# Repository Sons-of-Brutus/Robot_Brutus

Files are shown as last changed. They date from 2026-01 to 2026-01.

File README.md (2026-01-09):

# Robot Brutus

This repository contains the final project for the Mechatronics course, part of the Degree in Software Robotics Engineering at the Rey Juan Carlos University.

**Authors:** Sergio Sanchez Hernandez, Jorge Barroso Saugar, Sergio Cobos Blanco

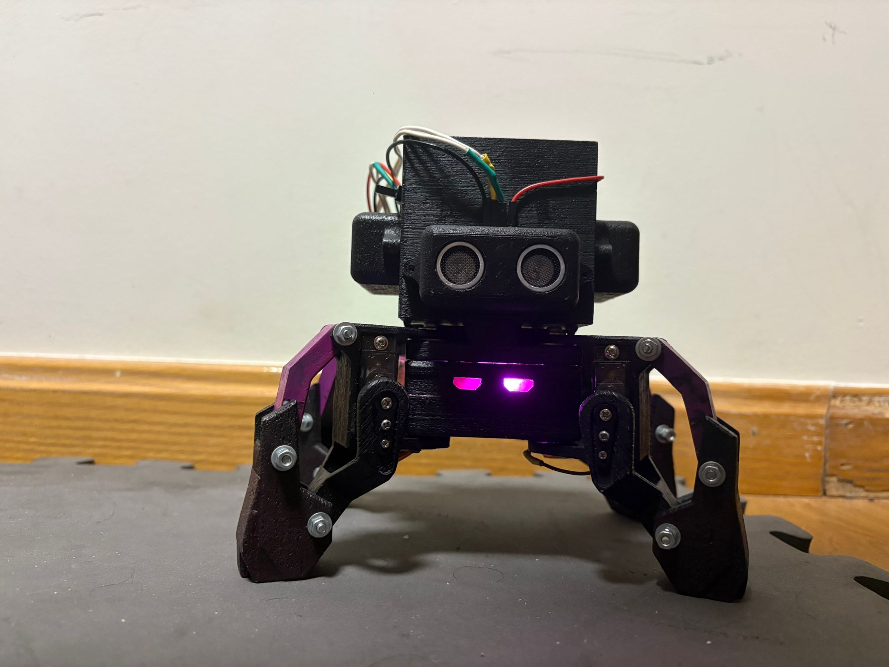
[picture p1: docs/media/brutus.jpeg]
BRUTUS


What can you find in this repository:
- [Technical report](./docs/brutus_technical_report.pdf)
- [User and mantainance manual](./docs/user_and_mantainance_manual.md)
- [Meshes of the pieces](./meshes/)
- [Code](./src/brutus_esp32)
- [Brutus' MQTT user interfaces](./mqtt_interface/)
- [Doxygen index of the code](https://sons-of-brutus.github.io/Robot_Brutus/)

---

Original design from thingiverse: https://www.thingiverse.com/thing:1265766/files

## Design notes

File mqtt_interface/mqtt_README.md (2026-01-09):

# mqtt_README

Brief guide to install Mosquitto and test MQTT topics (public broker: `test.mosquitto.org`).

## Requirements
- Debian/Ubuntu based system
- Internet connection (a public broker is used for testing)

## 1. Install Mosquitto and clients
```bash
sudo apt update
sudo apt install mosquitto mosquitto-clients -y
```

## 2. Subscribe to individual topics
Open a terminal for each subscriber (or multiplexer if you prefer).

ESP (topics published by the ESP32):
```bash
mosquitto_sub -h test.mosquitto.org -t brutus/data/heartbeat
mosquitto_sub -h test.mosquitto.org -t brutus/data/pose
mosquitto_sub -h test.mosquitto.org -t brutus/data/distance/front
mosquitto_sub -h test.mosquitto.org -t brutus/data/distance/right
mosquitto_sub -h test.mosquitto.org -t brutus/data/distance/left
```

Controller (topics received/monitored by the controller):
```bash
mosquitto_sub -h test.mosquitto.org -t brutus/cmd/mode
mosquitto_sub -h test.mosquitto.org -t brutus/cmd/velocity
mosquitto_sub -h test.mosquitto.org -t brutus/cmd/pose
```

## 3. Subscribe to all topics
Use the wildcard `#` to capture everything under `brutus/`:
```bash
mosquitto_sub -h test.mosquitto.org -t "brutus/#"
```

## 4. Publish test messages
Send test messages to verify callbacks and subscriptions.

Messages from the ESP (simulated):
```bash
mosquitto_pub -h test.mosquitto.org -t brutus/data/heartbeat -m "heartbeat"
mosquitto_pub -h test.mosquitto.org -t brutus/data/pose -m "data_pose"
mosquitto_pub -h test.mosquitto.org -t brutus/data/distance/front -m "sensor_front"
mosquitto_pub -h test.mosquitto.org -t brutus/data/distance/right -m "sensor_right"
mosquitto_pub -h test.mosquitto.org -t brutus/data/distance/left -m "sensor_left"
```

Messages from the controller:
```bash
mosquitto_pub -h test.mosquitto.org -t brutus/cmd/mode -m "cmd_mode"
mosquitto_pub -h test.mosquitto.org -t brutus/cmd/velocity -m "cmd_vel"
mosquitto_pub -h test.mosquitto.org -t brutus/cmd/pose -m "cmd_pose"
```

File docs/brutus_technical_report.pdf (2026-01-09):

# Brutus: Design and Implementation of a Quadruped Robot


Sergio Sanchez Hernandez, Jorge Barroso Saugar, Sergio Cobos Blanco

January 2026

1

## Contents

1 Introduction | 3
2 Structural Design | 3
3 Electronic design | 4
4 Software and control | 8
5 Software Implementation | 8
6 Simulation and Design Validation | 9
7 Experimental Results: Wall-Following Test | 10
8 Future Work and Proposed Improvements | 10

2

## 1 Introduction

This technical report details the design and implementation of the Brutus quadrupedal robot, providing an in-depth analysis of its structural design, hardware specifications, and FreeRTOS-based embedded software control.
The robot must meet the following specifications:
- Its dimensions must not exceed 30 × 30 × 30 cm.
- It must be powered by rechargeable batteries.
- The robot must feature a basic interface to start and stop its operation.

It must also pass the following two tests:

- Wall-Following Test: In less than 1 minute, the robot must move parallel to a flat wall, placed on either side of the robot, for at least 1 meter. Additionally, it must carry a 250-gram load.
- Obstacle Avoidance Test: In less than 2 minutes, the robot must be capable of avoiding obstacles while moving within a 2 × 2 meters area, reaching each of the adjacent walls. The robot starts from the center of the square.

## 2 Structural Design

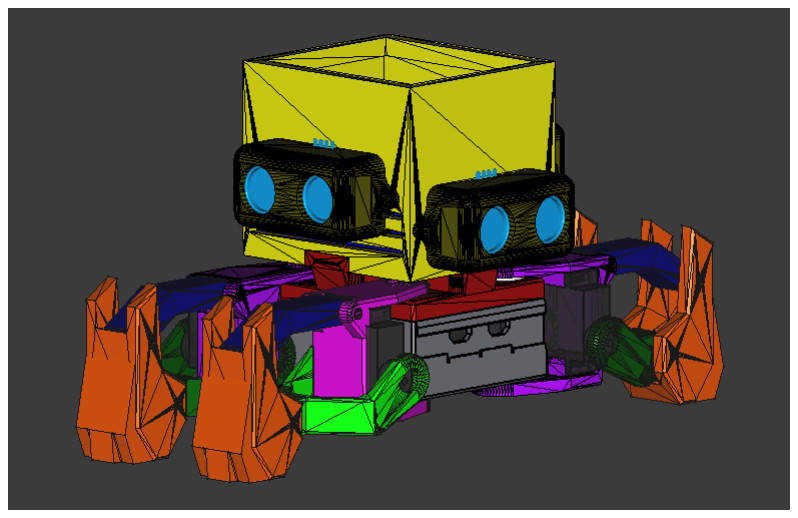
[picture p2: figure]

Figure 1: Full assembly of the Brutus robot in FreeCAD.

### 2.1 Design selection and justification

The design of Brutus is based on a model found on Thingiverse. (https://www.thingiverse.com/thing:1265766/files)

This design was selected for its compact footprint, ensuring full compliance with the size specifications and less effort for the servos at the joints. Additionally, the two degrees of freedom in each of the four legs allow for simplified control while maintaining high mobility standards.

3

One of the most remarkable features of this design is the parallel linkage mechanism incorporated into the legs. This configuration ensures that the foot remains perpendicular to the ground throughout its vertical range of motion. Consequently, onboard sensors are isolated from tilt variations along the X and Y axes, maintaining a stable reference frame during locomotion.

### 2.2 Comparison with Original Design

The original models underwent several aesthetic and practical modifications to suit the project requirements:

- Both the ’shoulders’ and the chassis were modified to accommodate MG90s servo motors.
- A custom top module was designed to house the power supply battery and circuit, and distance sensors.
- The chassis cover was redesigned to attach the upper module (upside) and the ESP32 (facing down).

### 2.3 Materials and Manufacturing

The structural components were manufactured using 3D printing. PLA was selected as the primary material due to its high tensile strength, ease of printing, and dimensional stability, which is critical for the alignment of the leg mechanisms.

## 3 Electronic design

### 3.1 Actuators

The selected actuators must therefore provide sufficient torque, adequate speed, electrical compatibility and acceptable size and weight.

The servos must be capable of:

- Supporting the weight of the robot and the load during the support phase of walking.
- Producing enough torque to lift and move the legs.
- Moving fast enough to generate a stable and smooth gait.
- Allow PWM control.

4

The robot uses MG90S micro servos for all leg joints. Small, lightweight, strong and fast-rotation actuators, which are a really good election for the robot.

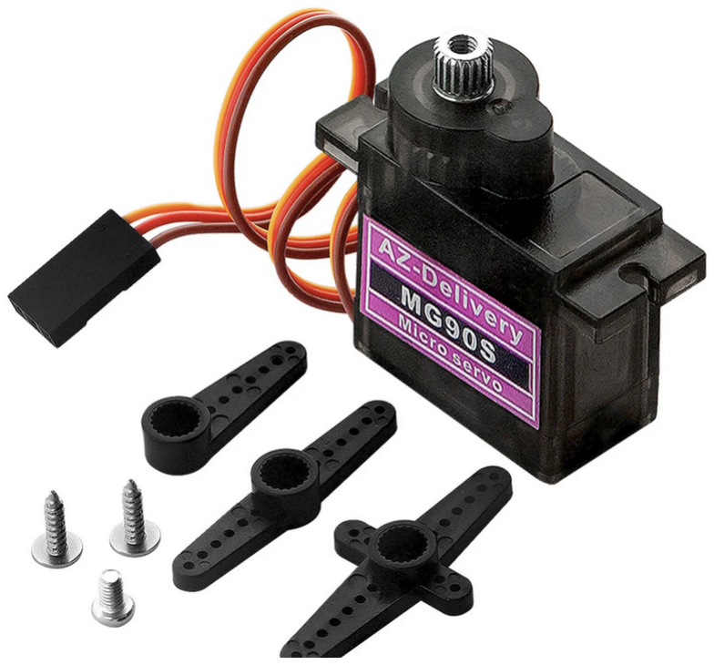
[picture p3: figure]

Figure 2: MG90s servo

The MG90S servo provides a nominal stall torque of approximately 1.86 kg · cm, which correspond to 0.1824 N
m .

The typical speed of this servos is 0.1 s/600◦
, so we know that they can reach 600◦/s ≈ 10.47 rad/s. This ensures that the simulated gait is realistic and achievable by the real servos. The MG90S provides sufficient speed to generate a smooth and stable walking motion without causing excessive inertia or oscillations.

The 8 servos are controlled using a PCA9685. This is a 16-channel, 12-bit PWM I2C-bus controlled driver that significantly offloads the processing work from the main microcontroller. By using this external driver, we can control all 8 servomotors using only two pins (SDA and SCL), which simplifies the wiring and ensures high-precision timing for the leg movements.

The final actuator is an RGB LED module, which serves as a visual diagnostic tool. This component enables real-time debugging by representing up to eight distinct color combinations, allowing for the intuitive monitoring of various system states and logic conditions.

### 3.2 Sensors

The sensors selected for resolving the exercises were the HC-SR04 for distance measurement. These are cost-effective ultrasonic sensors that operate by emitting high-frequency sound waves and measuring the time it takes for the echo to return after hitting an object.

5

With a detection range of ≈ 2 cm to 400 cm and an accuracy of ≈ 3 mm, this small sensors are ideal for the Wall-Following and Obstacle Avoidance tests. In our configuration, three sensors were mounted on the custom top module, facing front, left, and right, to provide a 180◦ field of view, allowing the Brutus robot to maintain a constant distance from the walls while simultaneously detecting potential collisions in its path.

### 3.3 Control unit

The ESP32-WROOM-32 was selected as the central processing unit due to its superior technical specifications. Its dual-core architecture enables the isolation of the gait control algorithm from perception and high-level logic tasks, ensuring stable locomotion. Integrated WiFi and Bluetooth connectivity facilitate remote commanding and real-time telemetry via an external web interface.

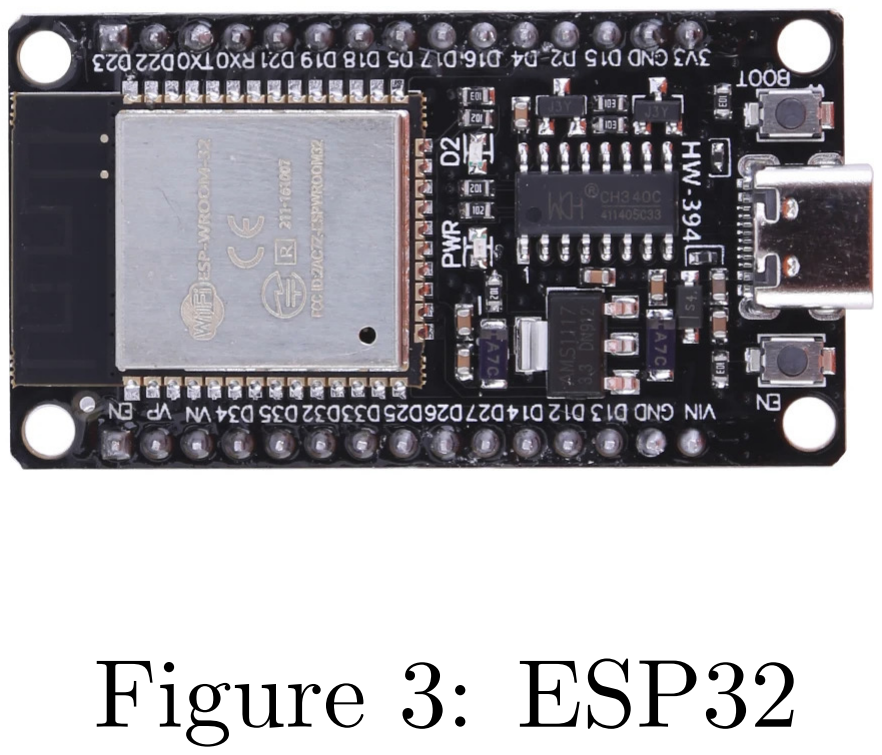
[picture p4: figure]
Figure 3: ESP32

Furthermore, its high clock speed and memory capacity provide a significant performance advantage over traditional platforms like Arduino UNO. The native support for FreeRTOS is crucial for implementing Brutus as a Real-Time System (RTS), allowing for deterministic task scheduling. Finally, its compact form factor ensures a seamless fit within the chassis constraints.

### 3.4 Power supply unit

Total current (peak and continuous) required by the system:

IT = IESP 32 + IHC−SR04 × 3 + ILED + IMG90s × 8 + IP CA9685

Ipeak ≈ 0.3 + 0.015 × 3 + 0.06 + 1.1 × 8 + 0.025 = 9.23 A
Icontinous ≈ 0.3 + 0.002 × 3 + 0.06 + 0.4 × 8 + 0.025 = 3.29 A

We want Brutus to operate for at least half an hour, so the minimum required capacity in the worst case must be:
qT = 9.23 A × 0.5 h = 4.615 Ah = 4615 mAh

These are the components (with their nominal voltage) which will be powered by the battery:

- ESP32 (5 V)

6

- PCA9685, and servos connected to it (5 V)
- HC-SR04 (5 V)

Our battery has to give 5 V.

The selected battery is a 3S1P Li-ion battery (12 V, 5200 mAh) was chosen because it satisfies all the electrical, power and autonomy requirements of the robot while remaining compact and lightweight. This battery has a discharge continous current of 5 A and a discharge peak current of 10 A.

If we consider the “worst case” as a sustained demand close to the battery’s continuous current rating:
Tworstcase(peak) = 5.2/9.23 = 0.56 h ≈ 33.6 min
Tworstcase(continuous) = 5.2/3.29 = 1.58 h ≈ 45.6 min

The battery provides a voltage range of 8.0 V to 12.6 V, so we choosed to use a DC-DC Buck Module to generate a stable 5 V supply for all electronics regardless of the battery’s state of charge.

### 3.5 Electronic Schematic

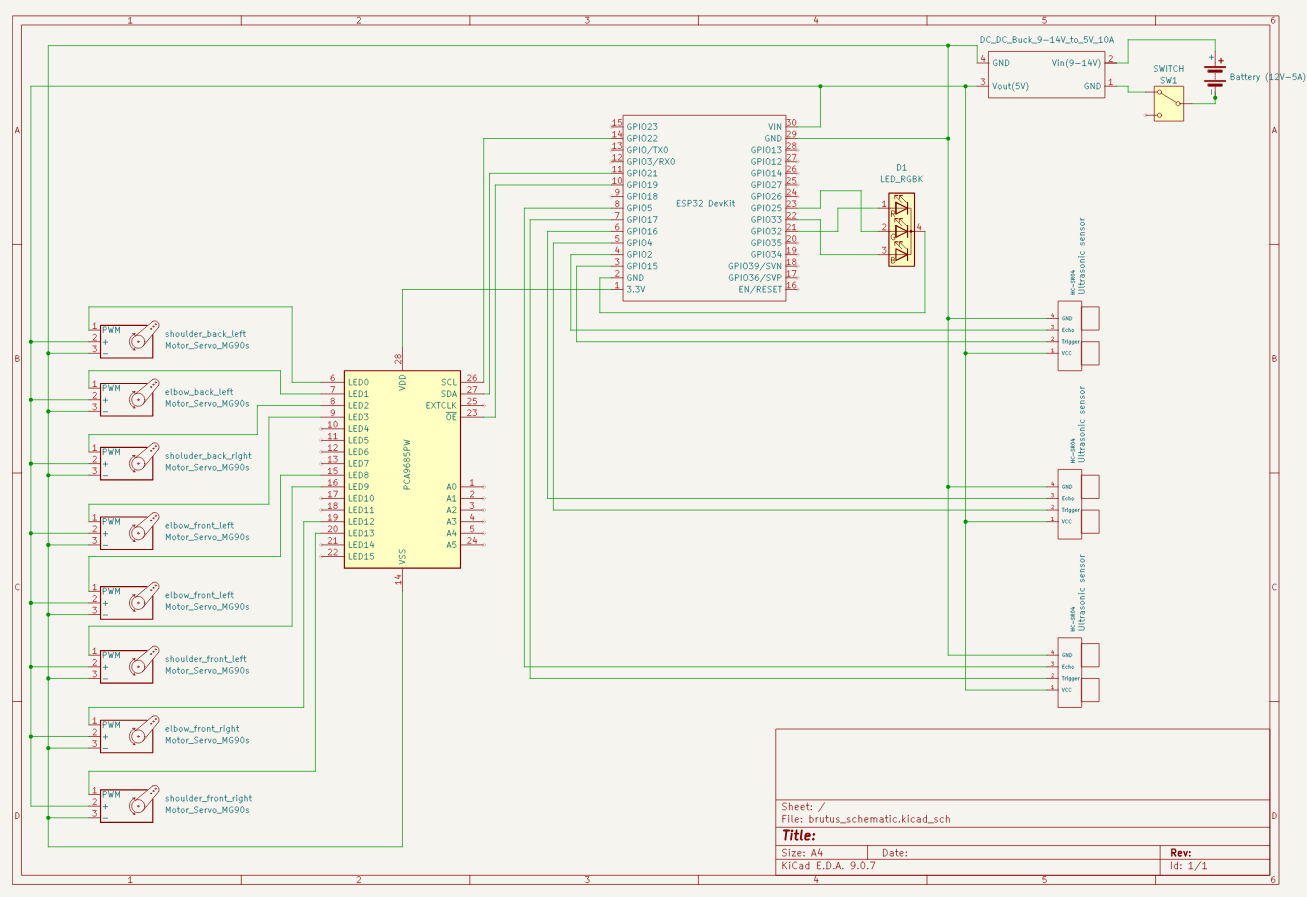
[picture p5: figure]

Figure 4: KiCad schematic of the circuit

7

## 4 Software and control

## 5 Software Implementation

The robot’s firmware is built upon FreeRTOS, enabling its operation as a Real-Time System (RTS) and ensuring deterministic execution of all critical tasks. Leveraging the dual-core architecture of the ESP32, the locomotion control is isolated on one core, while perception, high-level logic, and communication protocols run independently on the second.
The primary codebase is developed using Object-Oriented Programming (OOP) within the Arduino framework, establishing a modular and scalable architecture. The system is structured through the following specialized classes:
- Pca9685Servo.h: A low-level interface for direct pulse-width modulation (PWM) control via the PCA9685 driver.
- BrutusLegInterface.h: A kinematic abstraction layer for individual leg positioning (dependent on Pca9685Servo.h).
- BrutusPerception.h: This class manages the operation of the HC-SR04 ultrasonic sensors.
- Brutus.h: A comprehensive manager for the robot’s global state, coordinating all integrated actuators and sensors (dependent on BrutusLegInterface.h and BrutusPerception.h).
- BrutusComms.h: A dedicated interface for asynchronous MQTT-based communications.

### 5.1 Locomotion and Gait Algorithm

The locomotion strategy is based on a diagonal trot gait, characterized by a sequence of poses where two diagonal pairs of legs move in synchronization. While one pair performs the swing phase (moving through the air), the opposite pair executes the stance phase (contact with the ground), providing the necessary thrust to propel the chassis forward.
For high-level maneuvering, a velocity-based control scheme was implemented. This allows the system to translate linear velocity commands (vx) and angular velocity commands (ω) into coordinated joint movements:
- Translation: Achieved by modulating the step frequency and stride length.
- Rotation (Yaw Control): Instead of complex inverse kinematics, an efficient differential thrust method was used. By reducing the angular sweep (amplitude) of the ”shoulder” servos on the inner side of the turn, the outer legs generate a larger displacement vector, effectively pivoting the robot toward the desired direction.

8

### 5.2 Remote Interface and Telemetry

Brutus maintains a persistent connection to an MQTT broker, facilitating real-time telemetry, state switching, and remote commanding. To satisfy the requirement for a visual user interface, both a native Android application developed in Android Studio and a custom CLI (Command Line Interface) script were implemented, allowing for seamless interaction with the robot’s internal states.

### 5.3 Concurrency and Thread-Safety

Perception is handled by a periodic FreeRTOS task that samples ultrasonic distance data. To ensure data integrity in a multi-core environment, these values are accessed via thread-safe methods protected by Binary Semaphores (Mutexes). This synchronization mechanism prevents race conditions when the high-level logic task requests sensor data while the perception task is updating it. Similar protection is applied to the velocity command variables. The priorities for the multi-task core are: 1. Perception, 2. High-Level logic, 3. Communications.

## 6 Simulation and Design Validation

The primary objective of the simulation was to validate the robot’s stability, center of mass (CoM), and joint torque requirements through a detailed URDF model. Realistic mass and inertia properties were assigned to each link, including the external load on the top module, to ensure the physical design could withstand operational stresses and maintain coherent kinematics before manufacturing.
Due to the complexity of closed-loop
kinematic chains in physics engines,
the parallel linkage was simplified in the URDF while functionally maintaining foot perpendicularity. This causes a not really realistic analysis of the torques and the movement. The servomotors were modeled using position control with real-world torque and speed limits (600◦/s), enabling real-time logging to CSV files to verify that the selected actuators could handle peak loads during locomotion.

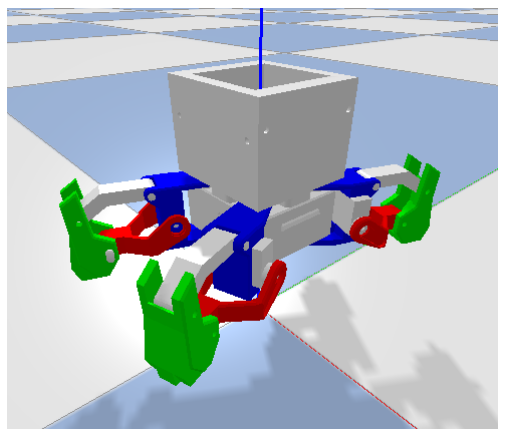
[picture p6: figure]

9

## 7 Experimental Results: Wall-Following Test

Figure 5 shows the optimal trial where the loaded robot traversed 1.6 meters. The right-hand sensor data reveals minor oscillations around the setpoint, caused by intrinsic noise, gait-induced mechanical shifts, and control logic tuning. Despite these fluctuations, the system demonstrated robust wall-following performance under loaded conditions.

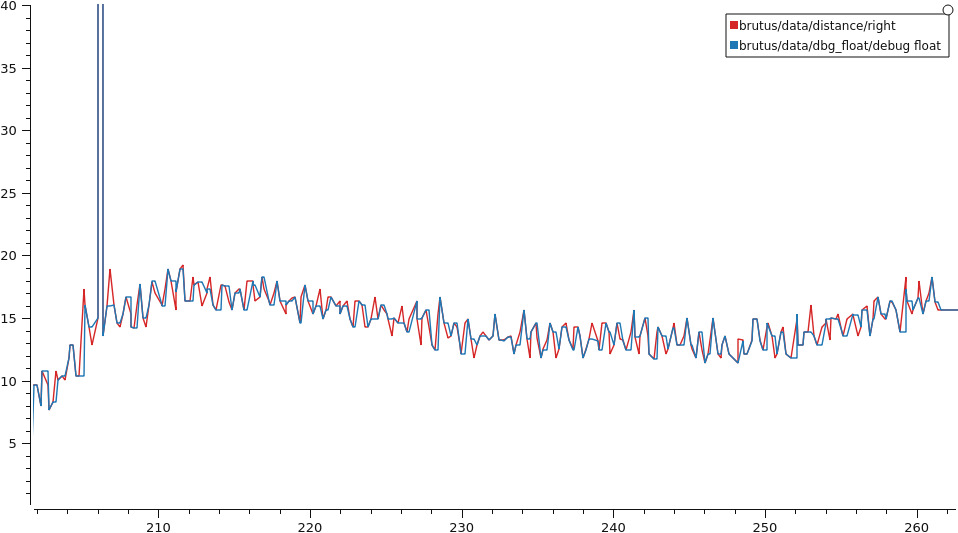
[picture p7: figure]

Figure 5: Ultrasonic sensor data during the 1.6-meter wall-following test.

## 8 Future Work and Proposed Improvements

- Sensor Fusion and Pose Estimation: Integrating an Inertial Measurement Unit (IMU) to implement filtering algorithms (such as a Kalman or Complementary filter). This would compensate for gait-induced oscillations during the swing phase and provide real-time data on the robot’s attitude (roll, pitch, and yaw), ensuring a stable reference frame for navigation.
- Active Perception (Scanning Radar): Mounting the ultrasonic sensors on dedicated micro-servos to implement an active scanning radar system. This configuration would significantly expand the Field of View (FoV), allowing for the generation of local occupancy maps and improving obstacle detection and path planning in complex environments.
- Structural Optimization for Serviceability: Expanding specific chassis sections to enhance thermal management through improved airflow. Additionally, redesigning the internal layout to increase accessibility, thereby facilitating assembly, cable routing, and routine maintenance procedures.

10

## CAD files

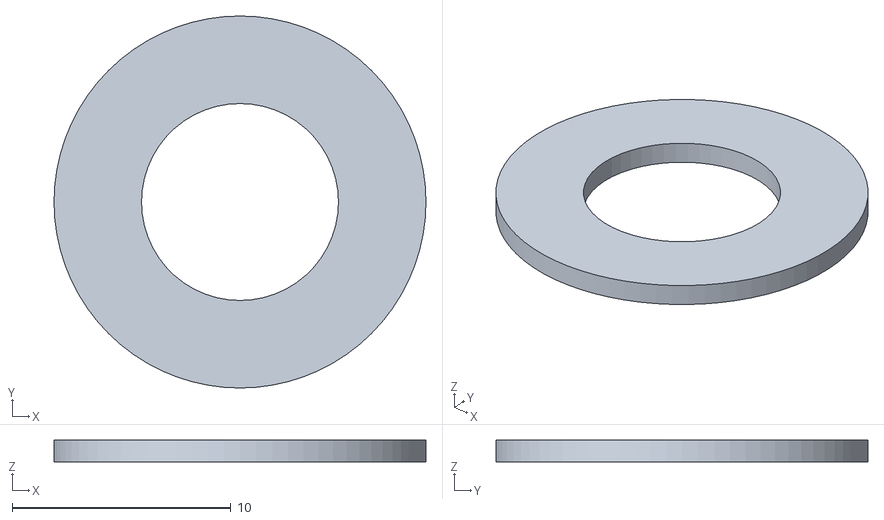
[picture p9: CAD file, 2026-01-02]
meshes/spacer.stl
17.0 x 17.0 x 1.00

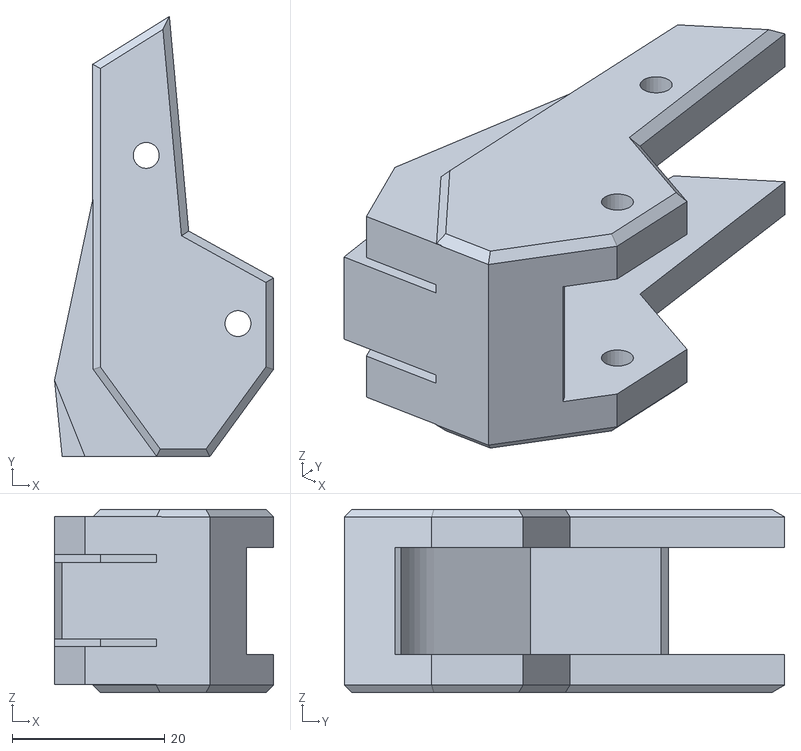
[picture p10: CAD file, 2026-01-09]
simulation/pybullet/model/meshes/foot_fist_mesh_relocated.stl
28.6 x 57.6 x 24.0

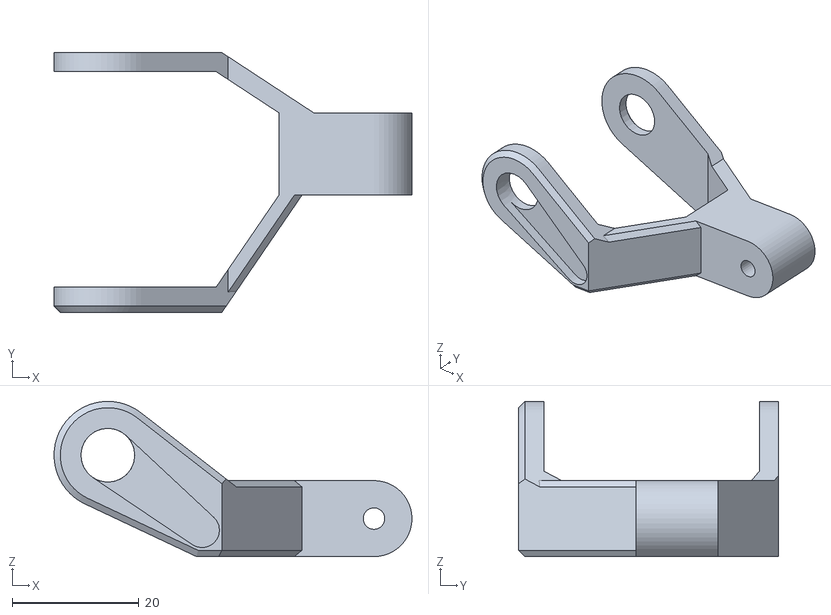
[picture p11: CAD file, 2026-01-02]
meshes/left_elbow_mesh.stl
56.5 x 41.0 x 24.5

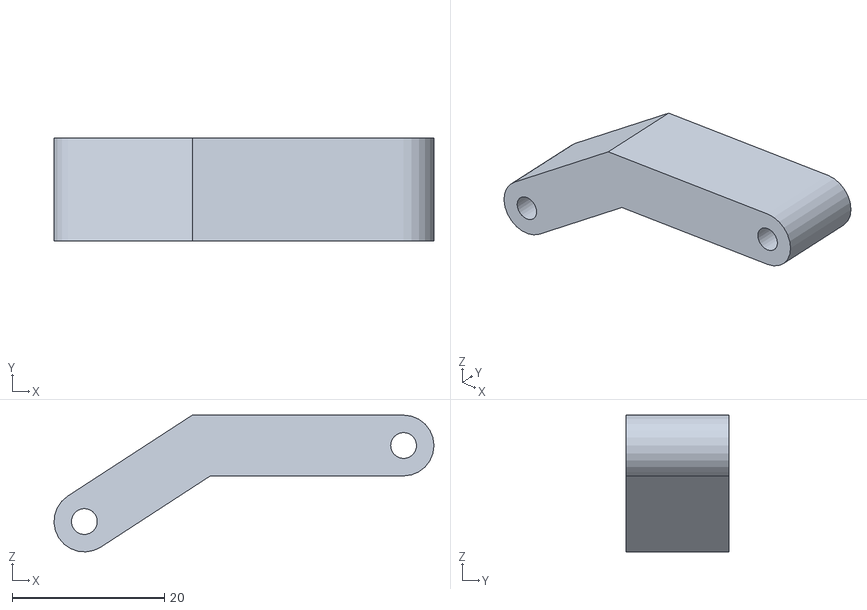
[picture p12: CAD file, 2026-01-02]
meshes/leg_up_link_mesh.stl
50.0 x 13.5 x 18.0

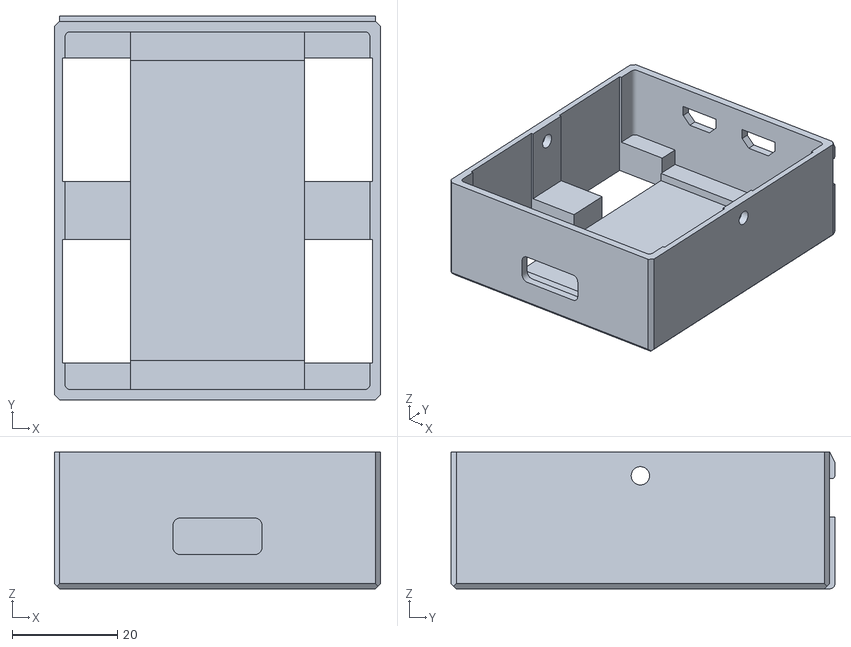
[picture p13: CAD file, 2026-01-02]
meshes/chasis_mesh.stl
62.0 x 73.0 x 26.0

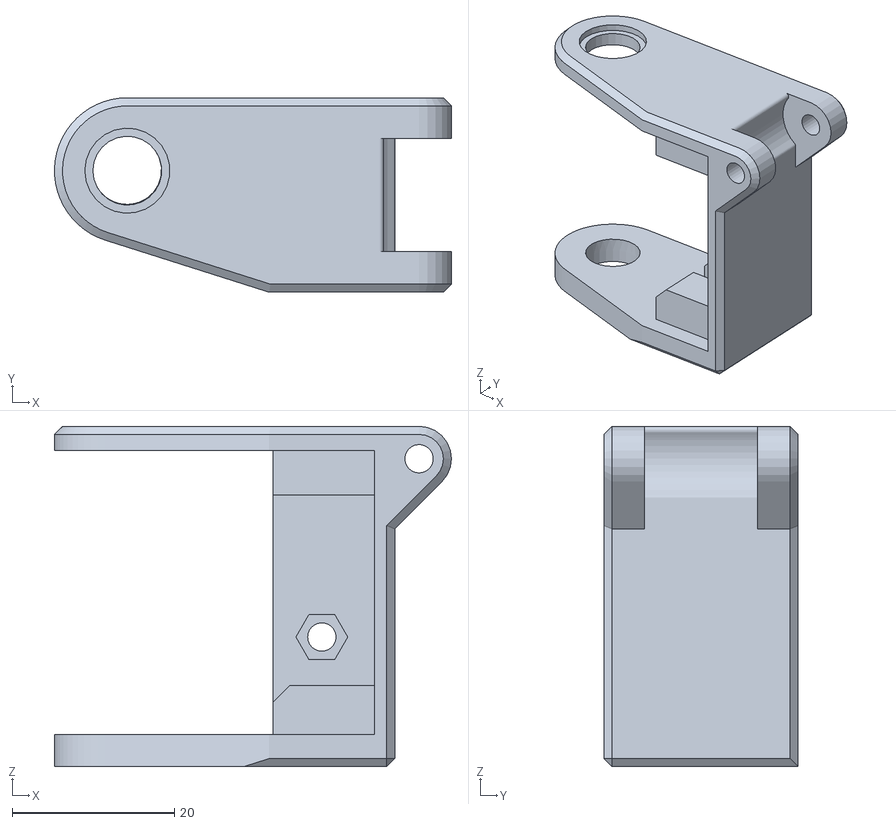
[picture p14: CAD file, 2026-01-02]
meshes/left_shoulder_mesh.stl
49.0 x 24.0 x 42.0

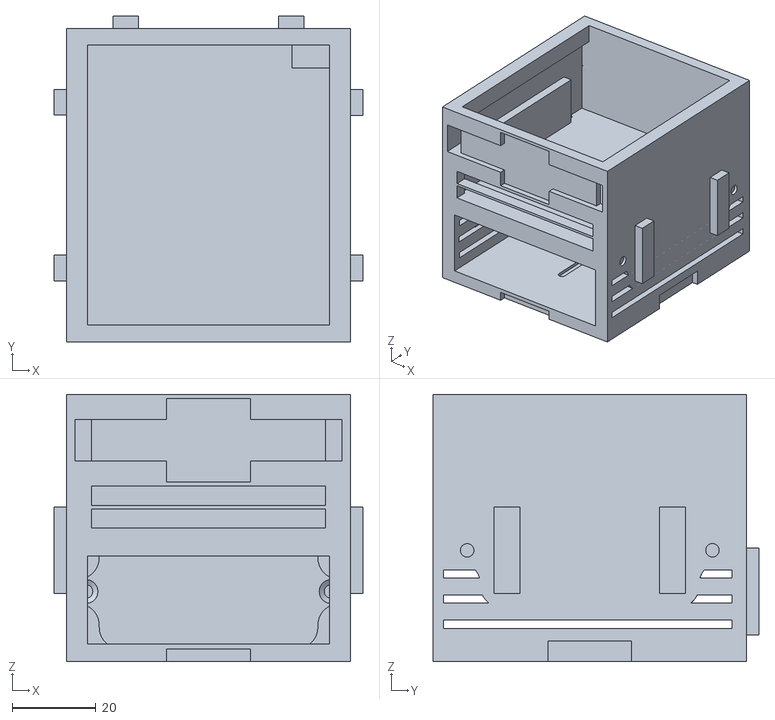
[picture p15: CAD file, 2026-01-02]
meshes/up_box_mesh.stl
73.9 x 78.0 x 64.0

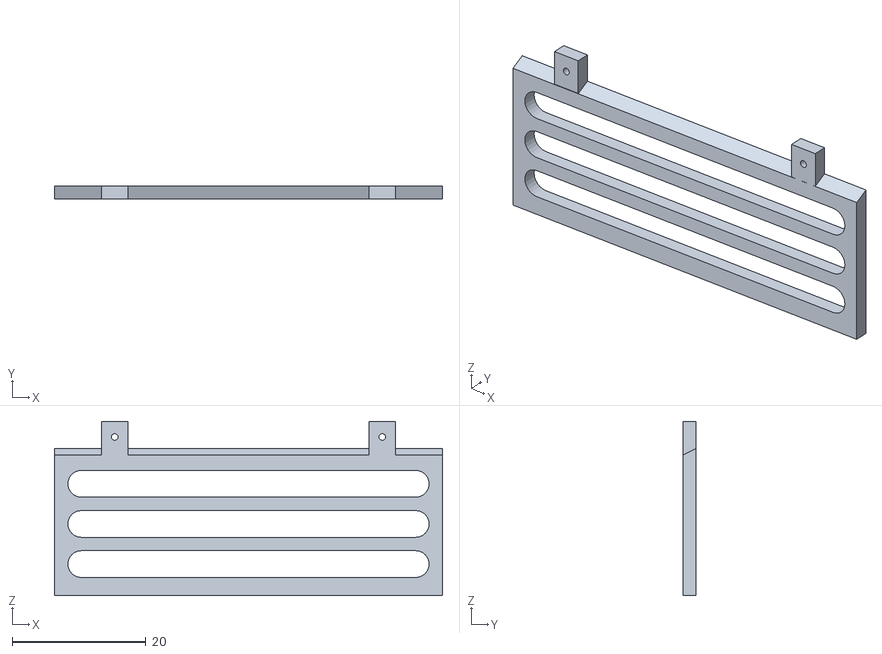
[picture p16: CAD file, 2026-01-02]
meshes/battery_limit_mesh.stl
58.0 x 2.00 x 26.1

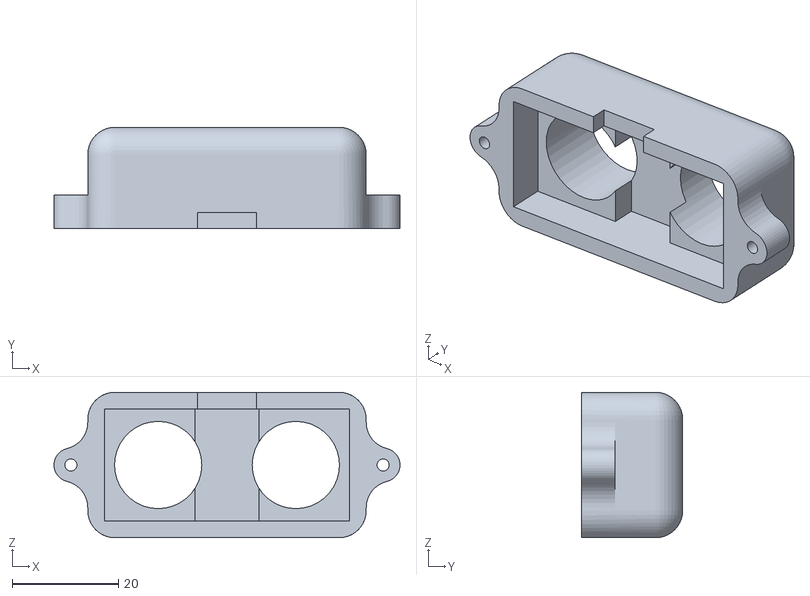
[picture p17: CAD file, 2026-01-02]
meshes/us_chasis_mesh.stl
65.0 x 19.1 x 27.3

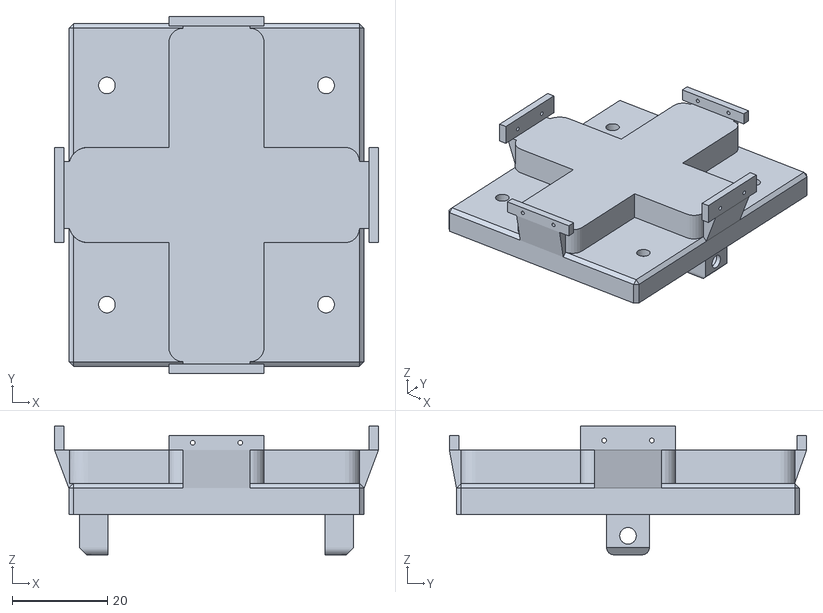
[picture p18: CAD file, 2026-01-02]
meshes/chasis_cover_mesh.stl
68.0 x 75.0 x 27.0

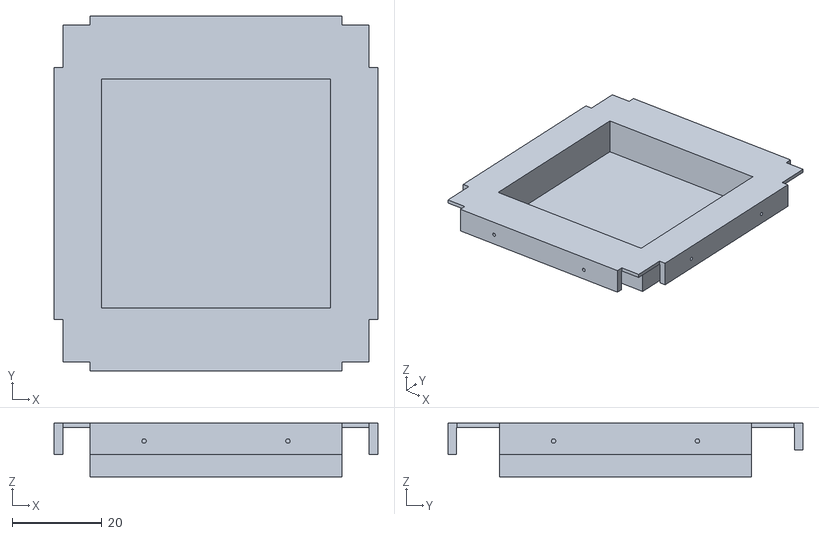
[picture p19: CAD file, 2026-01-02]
meshes/weight_case_mesh.stl
72.0 x 79.0 x 12.0

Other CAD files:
simulation/pybullet/model/meshes/foot_fist_mesh.stl
meshes/right_shoulder_mesh.stl
meshes/right_elbow_mesh.stl

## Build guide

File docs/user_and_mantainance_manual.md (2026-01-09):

# User and mantainance manual

---

## Table of content

This document is divided into the following sections:

1. [Mantainance manual](#mantainance-manual)
2. [Robot Components Overview](#robot-components-overview)
3. [Materials](#materials)
   1. [Printable pieces](#printable-pieces)
   2. [Electronic components](#electronic-components)
   3. [Wiring](#wiring)
   4. [Fasteners](#fasteners)
4. [Assembly](#assembly)
   1. [Soldering `ESP32` and `PCA9685` Connections](#1-soldering-esp32-and-pca9685-connections)
   2. [Assembling chasis (Part 1)](#2-assembling-chasis-part-1)
   3. [Assembling legs (Part 1)](#3-assembling-legs-part-1)
   4. [Connecting servos to `PCA9685`](#4-connecting-servos-to-pca9685)
   5. [Assembling chasis (Part 2)](#5-assembling-chasis-part-2)
   6. [Joining legs with chasis](#6-joining-legs-with-chasis)
   7. [Assembling upper box](#7-assembling-upper-box)
   8. [Joining upper box with chasis](#8-joining-upper-box-with-chasis)
   9. [Assembling legs (Part 2)](#9-assembling-legs-part-2)
5. [Mechanical Maintenance](#mechanical-maintenance)
   1. [Fasteners and Joint Inspection](#fasteners-and-joint-inspection)
   2. [Bearing Condition](#bearing-condition)
   3. [Servo Mounting and Horns](#servo-mounting-and-horns)
   4. [Printed Part Inspection](#printed-part-inspection)
6. [Battery Maintenance and Safety](#battery-maintenance-and-safety)
   1. [Voltage limits](#voltage-limits)
   2. [Storage recommendations](#storage-recommendations)
7. [Electrical Connections and Wiring Integrity](#electrical-connections-and-wiring-integrity)
   1. [Critical power cables](#critical-power-cables)
   2. [Connections most likely to cause power loss](#connections-most-likely-to-cause-power-loss)
   3. [Detecting bad contacts](#detecting-bad-contacts)
   4. [Ultrasonic sensor cables](#ultrasonic-sensor-cables)
8. [User Manual](#user-manual)
   1. [Network and MQTT configuration](#network-and-mqtt-configuration)
   2. [WiFi configuration](#wifi-configuration)
   3. [MQTT configuration](#mqtt-configuration)
9. [`brutus_params.h` – Robot configuration and motion parameters](#brutus_paramsh--robot-configuration-and-motion-parameters)
10. [`comms_params.h` – MQTT communication configuration](#comms_paramsh--mqtt-communication-configuration)
11. [User Sketch](#user-sketch)
12. [Logic Task Definition](#logic-task-definition)
13. [Doxygen](#doxygen)

---

# Mantainance manual

This document describes the recommended maintenance procedures for the Brutus quadruped robot.  
Its purpose is to ensure long-term reliability, safety, and performance by defining how the mechanical, electrical, and structural components should be inspected, cleaned, and replaced over time.

Brutus is a multi-servo quadruped robot built from 3D-printed structural parts, metal fasteners, electronic modules, and a Li-ion power system. Due to the presence of moving joints, electrical power distribution, and lithium batteries, proper maintenance is essential to prevent premature wear, electrical failures, and unsafe operating conditions.

This manual is based on:
- The mechanical assembly guide  
- The list of printed and electronic components  
- The electrical schematic (KiCad)  
- The battery and power system design  

It is intended for:
- Regular users performing routine checks  
- Developers modifying or upgrading the robot  
- Anyone disassembling and reassembling this robot  

The procedures described here allow safe servicing without damaging the robot.

---

## Robot Components Overview

Before performing any maintenance, inspection, or repair on Brutus, it is essential to understand the physical and electronic components that make up the robot.

This section provides a complete overview of all structural, mechanical, and electronic elements used in Brutus. Knowing the location, function, and role of each part allows safe and efficient troubleshooting, replacement, and upgrades.

---

## Materials

### Printable pieces
| Name | Quantity | Mesh | Image |
| :--- | :---: | :---: | ---: |
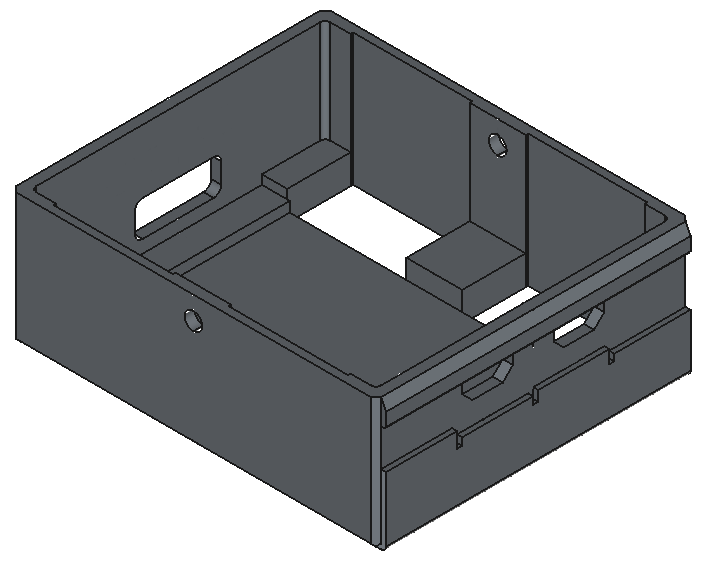
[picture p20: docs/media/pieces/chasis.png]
| `Chasis` | 1 | [chasis_mesh.stl](../meshes/chasis_mesh.stl) |  |
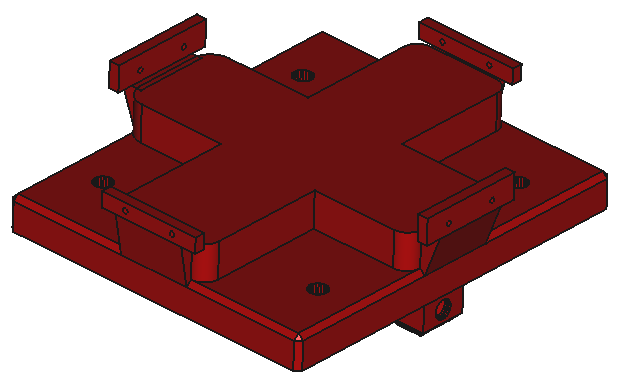
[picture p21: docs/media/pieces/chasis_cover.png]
| `Chasis cover` | 1 | [chasis_cover_mesh.stl](../meshes/chasis_cover_mesh.stl) |  |
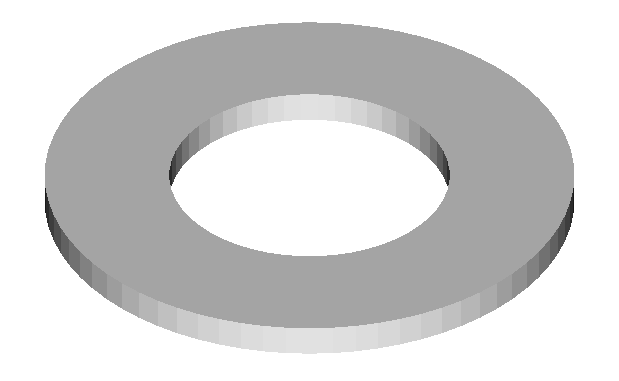
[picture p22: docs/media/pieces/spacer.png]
| `Spacer` (optional) | 4 | [spacer.stl](../meshes/spacer.png) |  |
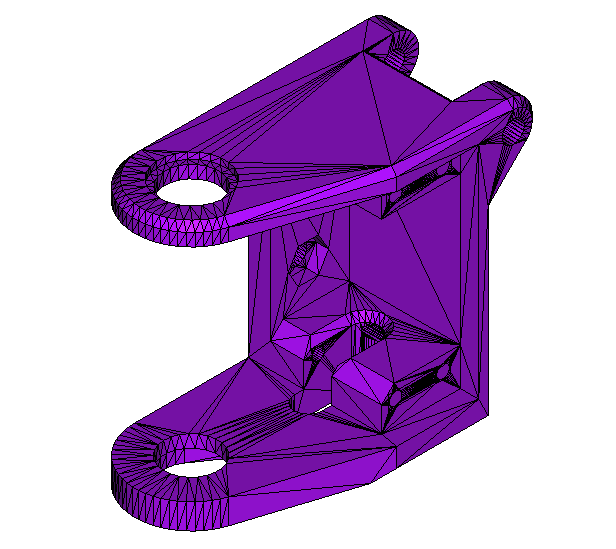
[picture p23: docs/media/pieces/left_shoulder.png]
| `Left shoulder` | 2 | [left_shoulder_mesh.stl](../meshes/left_shoulder_mesh.stl) |  |
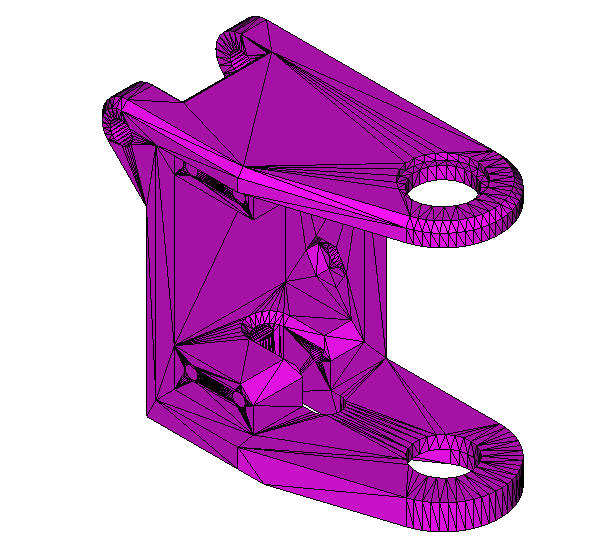
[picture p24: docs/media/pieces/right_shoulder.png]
| `Right shoulder` | 2 | [right_shoulder_mesh.stl](../meshes/right_shoulder_mesh.stl) |  |
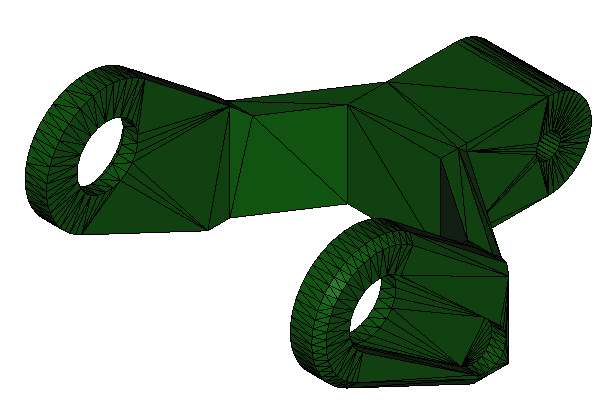
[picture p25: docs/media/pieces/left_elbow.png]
| `Left elbow` | 2 | [left_elbow_mesh.stl](../meshes/left_elbow_mesh.stl) |  |
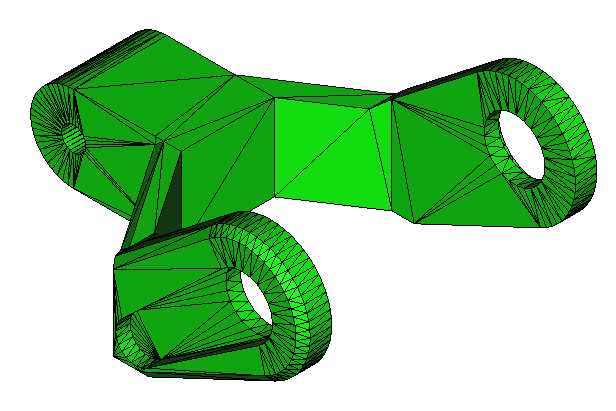
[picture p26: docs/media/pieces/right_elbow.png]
| `Right elbow` | 2 | [right_elbow_mesh.stl](../meshes/right_elbow_mesh.stl) |  |
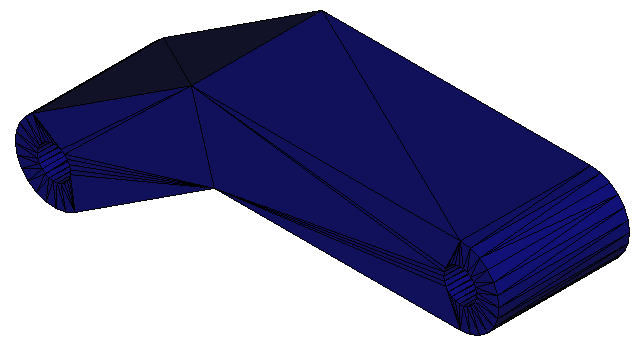
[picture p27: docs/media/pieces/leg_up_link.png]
| `Leg up link` | 4 | [leg_up_link_mesh.stl](../meshes/leg_up_link_mesh.stl) |  |
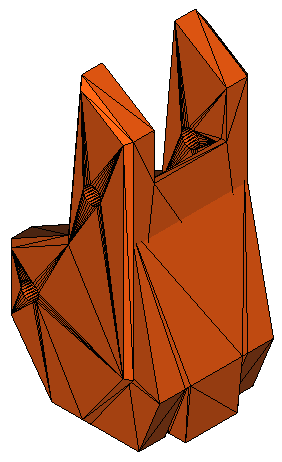
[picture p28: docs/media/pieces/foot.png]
| `Foot` | 4 | [foot_fist_mesh.stl](../meshes/foot_fist_mesh.stl) |  | 
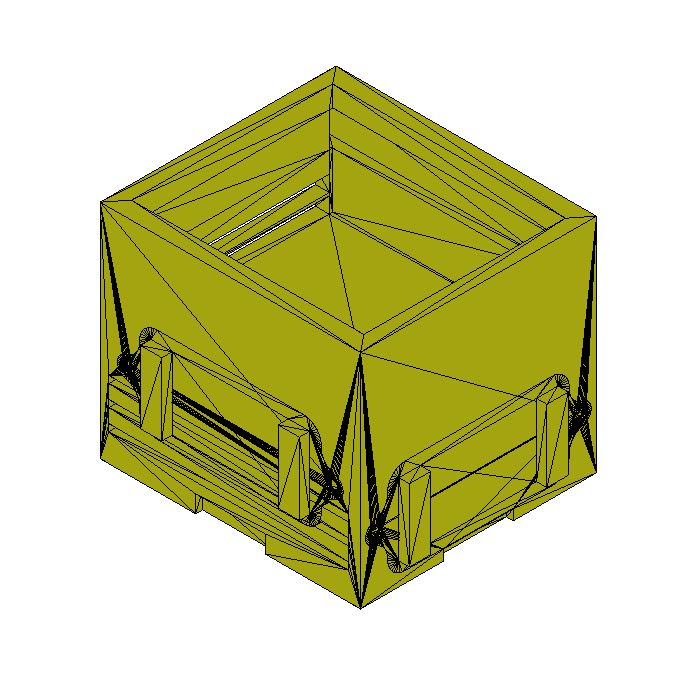
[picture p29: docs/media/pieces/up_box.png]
| `Up box` | 1 | [up_box_mesh.stl](../meshes/up_box_mesh.stl) |  |
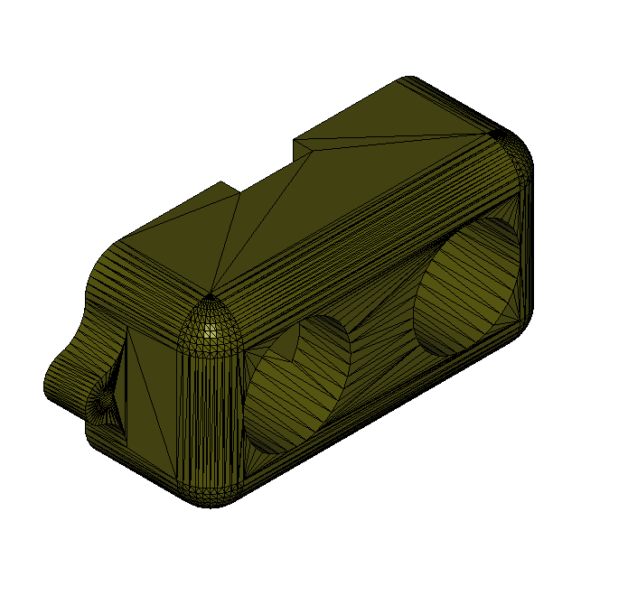
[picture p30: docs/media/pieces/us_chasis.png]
| `US Sensor chasis` | 3 | [us_chasis_mesh.stl](../meshes/us_chasis_mesh.stl) |  |
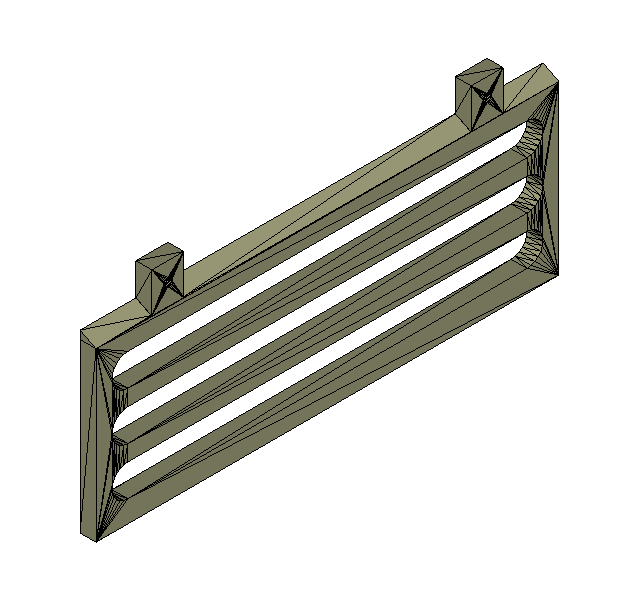
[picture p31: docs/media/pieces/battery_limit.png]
| `Battery limit` | 1 | [battery_limit.stl](../meshes/battery_limit.stl) |  |
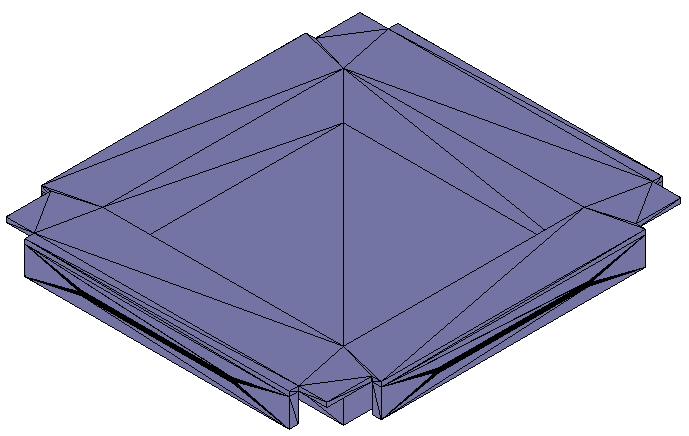
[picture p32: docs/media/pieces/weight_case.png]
| `Weight case` | 1 | [weight_case.stl](../meshes/weight_case.stl) |  |

**Notes:**
- ***Left shoulder/elbow** are for **front left** leg and **back right** leg, while **right shoulder/elbow** are for **front right** leg, **back left** leg.*
- *Spacer is optional as you can replace it for M3 metalic washers with similar dimensions.*

### Electronic components
| Name | Quantity | Description | Link | Image |
| :--- | :---: | :---: | :---: | ---: |
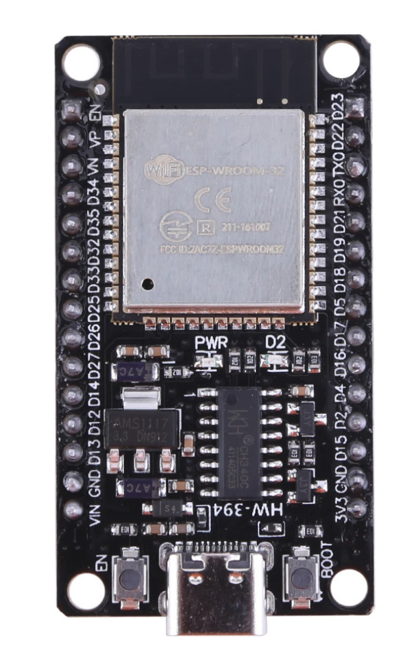
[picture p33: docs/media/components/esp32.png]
| `ESP32` development board | 1 | Dual-Core microcontroller with integrated WiFi and Bluetooth | [Link](https://www.amazon.es/AZDelivery-ESP-32-Dev-Kit-Development/dp/B0DJ33NNRD?) |  |
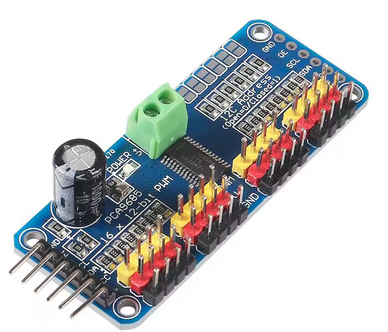
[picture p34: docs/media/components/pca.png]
| `PCA9685` | 1 | 16-channel, I2C-controlled PWM (Pulse Width Modulation) controller. For servos control. | [Link](https://es.aliexpress.com/item/1005005670283526.html) |  |
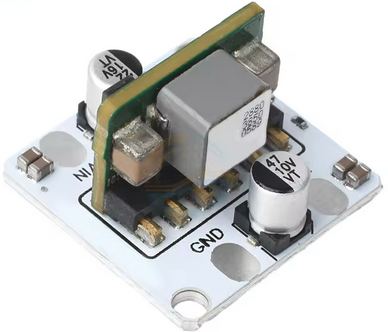
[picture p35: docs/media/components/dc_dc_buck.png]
| `DC-DC Buck module` | 1 | Ultra-small 10A DC-DC Buck Converter 9V-14V to 5V Step-Down Voltage Regulator Module. | [Link](https://es.aliexpress.com/item/1005009068963636.html?) |  |
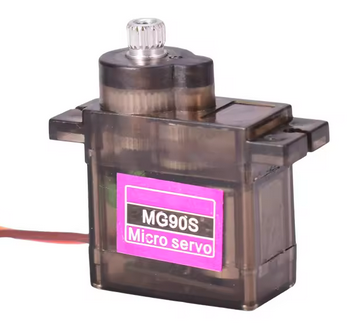
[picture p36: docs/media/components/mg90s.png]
| `MG90S Servo` | 8 | High-torque, metal-gear micro servo motor. | [Link](https://es.aliexpress.com/item/1005007522665750.html?) |  |
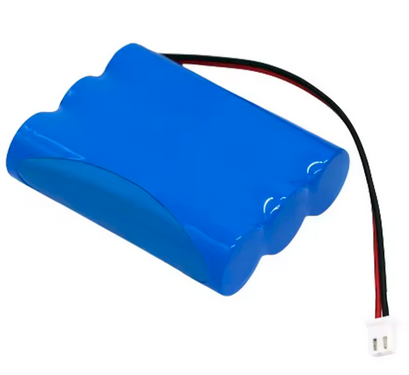
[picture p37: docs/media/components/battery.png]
| `Battery` | 1 | 3S1P 18650 Lithium-ion Battery Packs, 12V Rechargeable Lithium Battery.  | [Link](https://es.aliexpress.com/item/1005009656713743.html?) | 
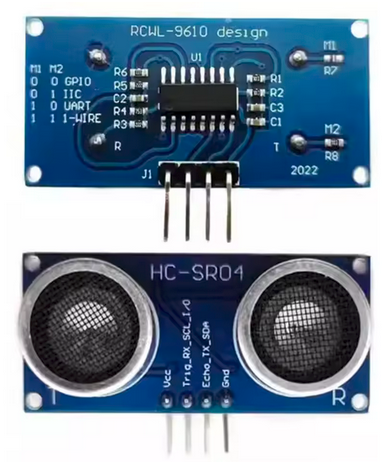
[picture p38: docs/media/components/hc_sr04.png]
| `HC-SR04` | 3 | Ultrasonic distance sensor | [Link](https://es.aliexpress.com/item/1005010356855481.html?) |  |
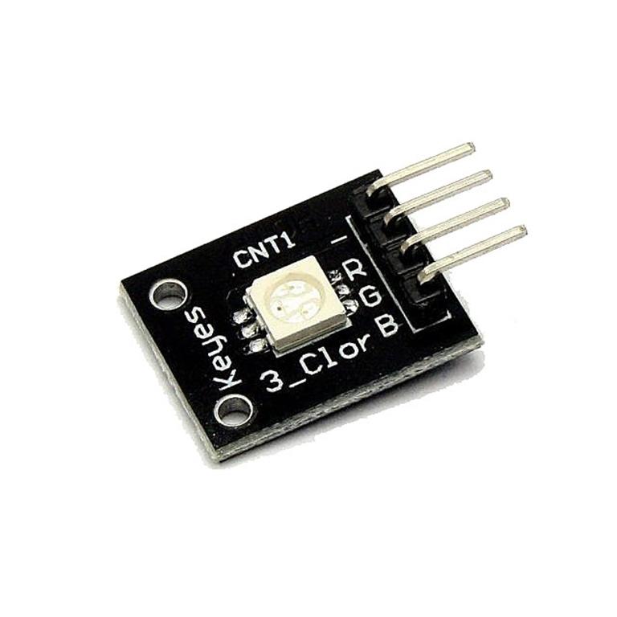
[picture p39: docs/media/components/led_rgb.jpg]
| `RGB LED` | 1 | RGB flat led module | Not specified |  |
| `Switch` | 1 | Electronic switch (as small as you can) | Not specified | Not specified |

### Wiring

**Important**: Some wire lengths are redundant.

| Name | Quantity/Length | Image |
| :--- | :----: | ---: |
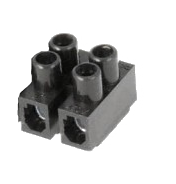
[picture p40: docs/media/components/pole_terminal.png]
| `2-Pole Terminal Block` | 1 |  |
| `16 AWG Wire` | 500 mm aprox. | - |
| `20 AWG Wire` | 500 mm aprox. | - |
| `26 AWG Wire` | 500 mm aprox. | - |
| `28 AWG Wire` | 200 mm aprox. | - |
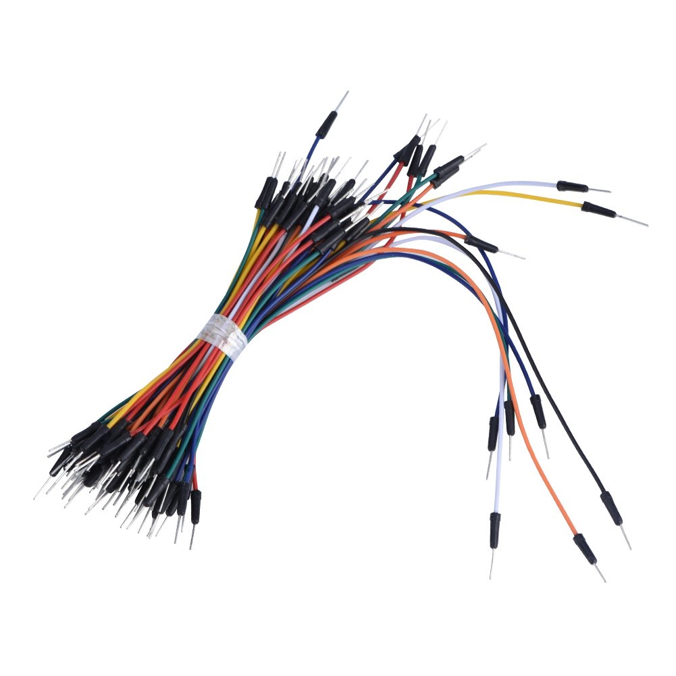
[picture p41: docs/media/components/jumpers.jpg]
| `Female-to-female jumper wire` | 18 | 

**Notes**:
- `2-Pole Terminal` can be substituted by:
  + Using 2 `1-Pole Terminal Block`.
  + Cutting a `N-pole Terminal Block` with more than 2 poles.
- You can substitute 28 AWG cables by using *jumper wires* with their conectors removed.
- Wire gauges:
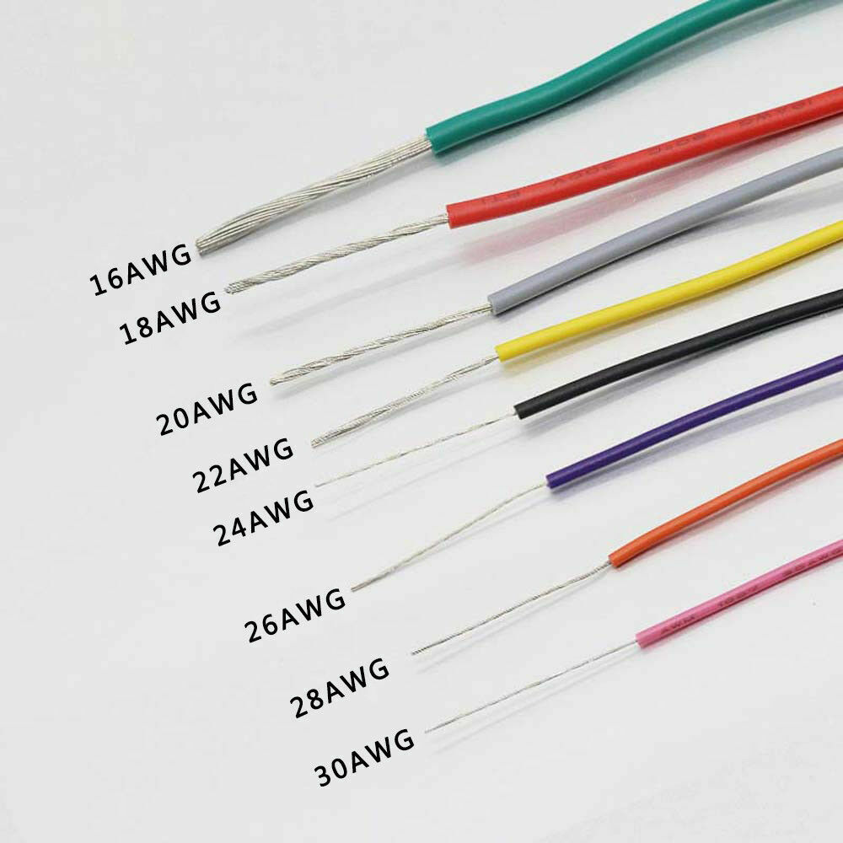
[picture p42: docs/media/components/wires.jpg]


### Fasteners

| Name | Details | Quantity | Image |
| :--- | :--- | :---: | ---: |
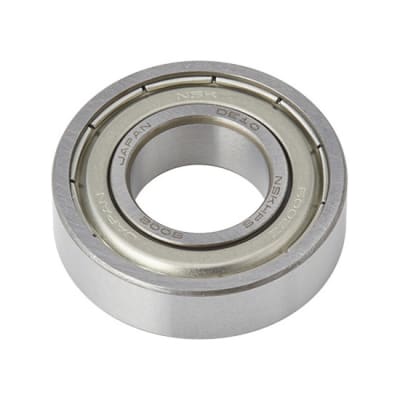
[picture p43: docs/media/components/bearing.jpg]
| `Bearing` | F693ZZ Bearing | 8 |  |
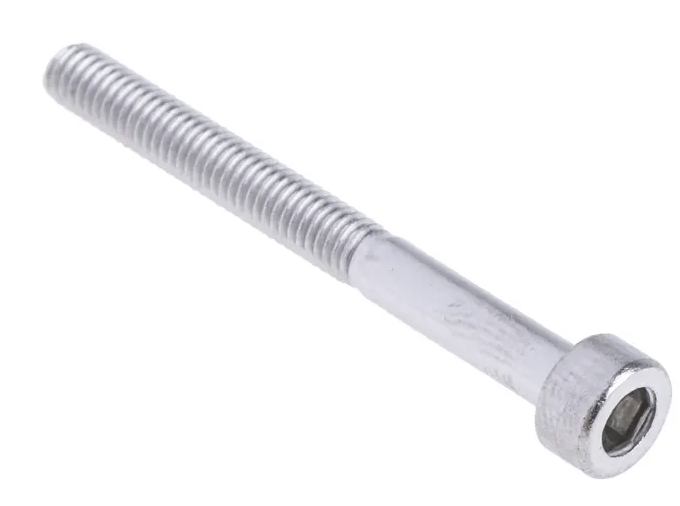
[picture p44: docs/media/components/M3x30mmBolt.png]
| `M3x30mm Bolt` | M3 30mm hex bolt | 12 |  |
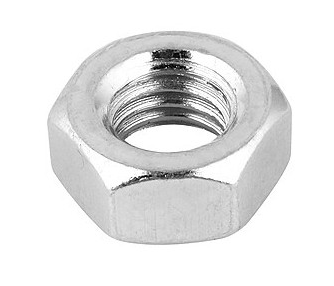
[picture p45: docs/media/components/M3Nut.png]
| `M3 Nut` | Standard M3 hex nut (used in legs + top cover) | 30 | |
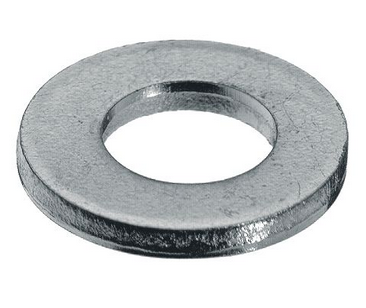
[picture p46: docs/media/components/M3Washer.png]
| `M3 Washer` | M3 metal washer | 16 |  |
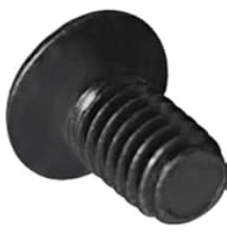
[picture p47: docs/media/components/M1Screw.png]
| `M1 Screw` | M1 self-tapping screw (servo horn screws + ESP top cover mount) | 10 |  |
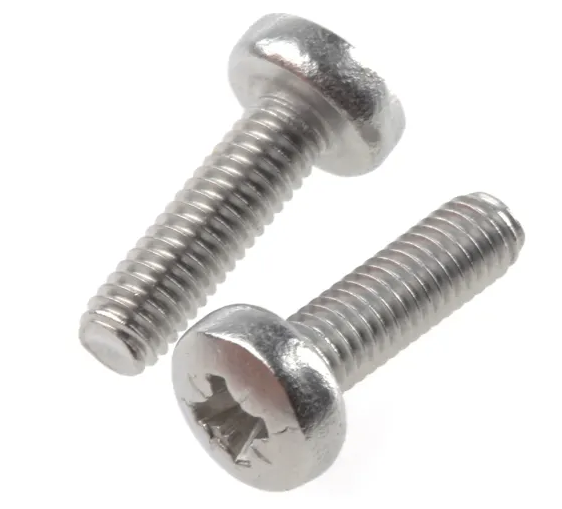
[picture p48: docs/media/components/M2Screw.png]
| `M2 Screw` | M2 screw (mounting servos, 2 per servo × 4 servos) | 8 |  |

---

## Assembly
Naw we are going to describe the complete mechanical and electrical assembly process of the Brutus quadruped robot.  
It provides step-by-step instructions for building the robot starting from individual electronic boards, servos, and 3D-printed parts up to a fully assembled and operational system.

The assembly process combines:
- Mechanical construction using 3D-printed structural components
- Electrical wiring and soldering of the control electronics
- Power distribution through a regulated battery system
- Integration of sensors, actuators, and control boards

This manual assumes that the user has:
- Basic experience with soldering and electronics
- Access to common tools (screwdrivers, soldering iron, cutters, etc.)
- The printed parts and electronic components listed in the Materials section

Once assembled, the robot should match the mechanical and electrical configuration used during simulation and software development, ensuring that calibration, control, and power limits behave as expected.

---

This assembly instructions are divided in N parts:
1. [Soldering `ESP32` Connections](#1-soldering-esp32-connections)
2. [Assembling chasis (Part 1)](#2-assembling-chasis-part-1)
3. [Assembling legs (Part 1)](#3-assembling-legs-part-1)
4. [Connecting servos to `PCA9685`](#4-connecting-servos-to-pca9685)
5. [Assembling chasis (Part 2)](#5-assembling-chasis-part-2)
6. [Joining legs with chasis](#6-joining-legs-with-chasis)
7. [Assembling upper box](#7-assembling-upper-box)
8. [Joining upper box with chasis](#8-joining-upper-box-with-chasis)
9. [Assembling legs (Part 2)](#9-assembling-legs-part-2)

---
### 1. Soldering `ESP32` and `PCA9685` Connections

First of all, if your `ESP32` and/or `PCA9685` have soldered pins, first, you should desolder them, so the pin's holes for the upcoming cables are free.

Following the [electronics schematics image](../electronics/brutus_schematic/brutus_electronic_schematics.svg) (<-- Click here to see it bigger):


**Important**: Below the table there are important considerations you must take in account while soldering.

Solder the following connections:
| PIN 1 | PIN 2 | Wire | Details |
| :--- | :---: | :---: | ---: |
| `ESP32` Vin or 5V | *Nowhere* | 26 AWG | Leave a relatively large quantity of wire as it will be connected to the `2-Pole Terminal Block` at the upper box. Continued at "[Joining upper box with chasis](#joining-upper-box-with-chasis)" steps. |
| `ESP32` GND | *Nowhere* | 26 AWG | Leave a relatively large quantity of wire as it will be connected to the `2-Pole Terminal Block` at the upper box. Continued at "[Joining upper box with chasis](#joining-upper-box-with-chasis)" steps. |
| `PCA9685` V+ | *Nowhere* | 20 AWG | Leave a relatively large quantity of wire as it will be connected to the `2-Pole Terminal Block` at the upper box. Continued at "[Joining upper box with chasis](#joining-upper-box-with-chasis)" steps. |
| `PCA9685` GND | *Nowhere* | 20 AWG | Leave a relatively large quantity of wire as it will be connected to the `2-Pole Terminal Block` at the upper box. Continued at "[Joining upper box with chasis](#joining-upper-box-with-chasis)" steps. |
| `PCA9685` VCC | `ESP32` 3.3V | 28 AWG | - |
| `PCA9685` SCL | `ESP32` GPIO 22 | 28 AWG | It is **ESSENTIAL** that this connection doesn't change, `PCA9685`'s SCL needs to be connected to `ESP32`'s GPIO 22 |
| `PCA9685` SDA | `ESP32` GPIO 21 | 28 AWG | It is **ESSENTIAL** that this connection doesn't change, `PCA9685`'s SCL needs to be connected to `ESP32`'s GPIO 22 |
| `PCA9685` OE | `ESP32` GPIO 19 | 28 AWG | - |
| `RGB LED` R | `ESP32` GPIO 32 | 28 AWG | - |
| `RGB LED` G | `ESP32` GPIO 25 | 28 AWG | - |
| `RGB LED` B | `ESP32` GPIO 33 | 28 AWG | - |
| `RGB LED` GND | `ESP32` GND | 28 AWG | **VERY IMPORTANT!** This `ESP32` GND pin must not be the same as the one in the 2nd row of this table. |
| `ESP32` GPIO 2 | *Nowhere* | Female-to-female jumper | Cut and strip one of the ends of the wire. It needs a relatively large quantity of wire as it will be connected to one of the `HC-SR04` at the upper box. Connections at "[Joining upper box with chasis](#joining-upper-box-with-chasis)" steps. |
| `ESP32` GPIO 15 | *Nowhere* | Female-to-female jumper | The same as `ESP32` GPIO 2 |
| `ESP32` GPIO 16 | *Nowhere* | Female-to-female jumper | The same as `ESP32` GPIO 2 |
| `ESP32` GPIO 4 | *Nowhere* | Female-to-female jumper | The same as `ESP32` GPIO 2 |
| `ESP32` GPIO 17 | *Nowhere* | Female-to-female jumper | The same as `ESP32` GPIO 2 |
| `ESP32` GPIO 5 | *Nowhere* | Female-to-female jumper | The same as `ESP32` GPIO 2 |

**Considerations:**
- The wires for the 4 connections between `ESP32` and `PCA9685` should be *long enough* to allow the `chasis cover` to be separated slightly from the `chasis` when it is open, but *short enough* to avoid taking up excess space when closed.
- The 4 wires that connect `RGB LED` and `ESP32` should be long enough to place this two components as explained in "[Assembling chasis (Part 2)](#assembling-chasis-part-2)" steps.
- For each of the 6 wires for `HC-SR04`, you must remove one of the tips of a `Female-to-female jumper`. The removed part is the one soldered to the `ESP32` and the *female* part will be connected to the `HC-SR04`.

---
### 2. Assembling chasis (Part 1)

#### 2.1. `PCA9685` attachment in the chasis
Put the `PCA9685` in the space at the bottom center of the `chasis` as it is placed in the image:

<p align="center">
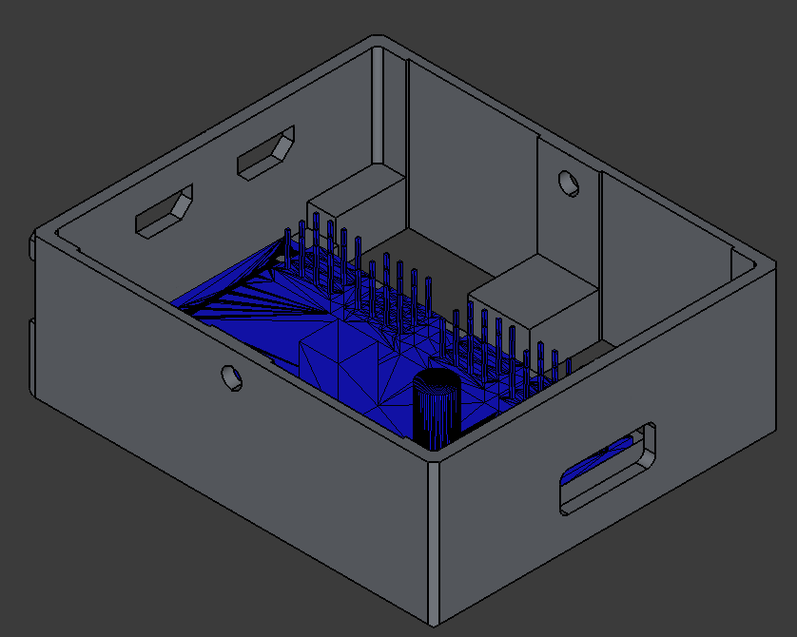
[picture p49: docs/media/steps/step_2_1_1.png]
  
</p>

#### 2.2. Trim the servo wires to fit
All 8 servos will have shorter wires, but in this step we will only consider the 4 servos inside the chasis.

1. Estimate the length of the servo wire. (At least enough to fit in the chasis)
```
 -------            Wire (PWM, GND, VCC)             -----------
|       |-------------------------------------------|           |
| Servo |-------------------------------------------| Connector |
|       |-------------------------------------------|           |
 -------                                             -----------
              |_____________________________|
                        📏 (Excess)

```
2. Cut out the excess section of wire estimated in the previous step.
```
 -------                    Excess Wire                    -----------
|       |------✂️ ---------------------------- ✂️---------|           |
| Servo |------✂️ ---------------------------- ✂️---------| Connector |
|       |------✂️ ---------------------------- ✂️---------|           |
 -------                                                   -----------
```
3. Now solder the servo-side wires to the connector-side wires.
```
 -------                  -----------
|       |-------🧑‍🏭-------|           |
| Servo |-------🧑‍🏭-------| Connector |
|       |-------🧑‍🏭-------|           |
 -------                  -----------
```

#### 2.3. Place the servos in the chasis

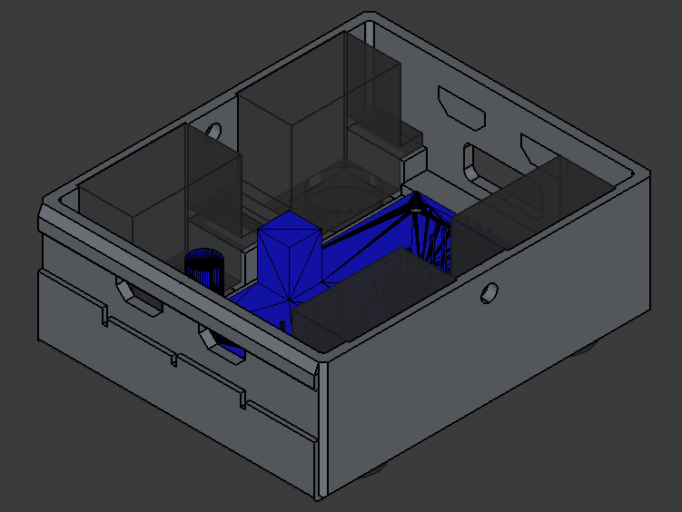
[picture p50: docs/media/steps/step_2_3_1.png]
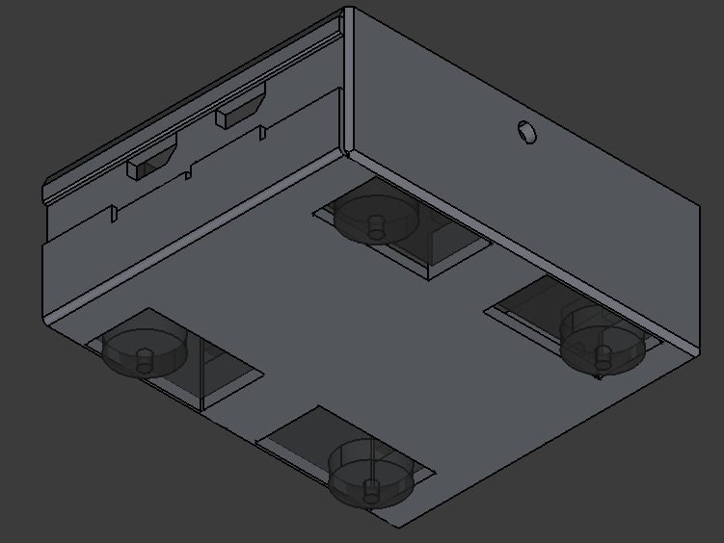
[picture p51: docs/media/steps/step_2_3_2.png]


You can use the `sheet metal screws` that are included with the servos to attach the servos to the chasis.

---
### 3. Assembling legs (Part 1)

The images are using `Left shoulder` and `Left elbow` pieces, but the same process is applied to `Right shoulder` and `Right elbow`.

#### 3.1. Attach the servo to the shoulder

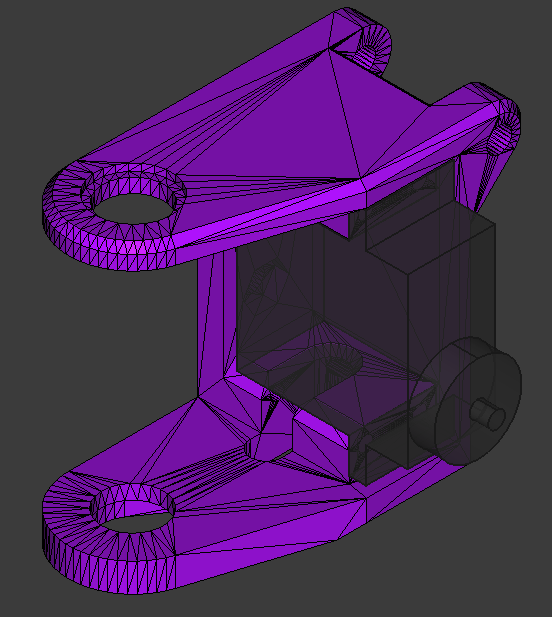
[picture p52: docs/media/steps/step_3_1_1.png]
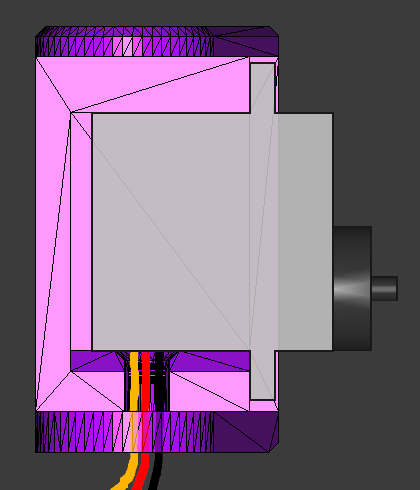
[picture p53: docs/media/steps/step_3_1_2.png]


You can use the `sheet metal screws` that are included with the servos to attach the servo to the shoulder.

**Important:** You should do the [same process off trimming the servo's wires](#22-trim-the-servo-wires-to-fit) so they could enter to the chasis and be connected to the `PCA9685`, letting some length for shoulder movement.

<p align="center">
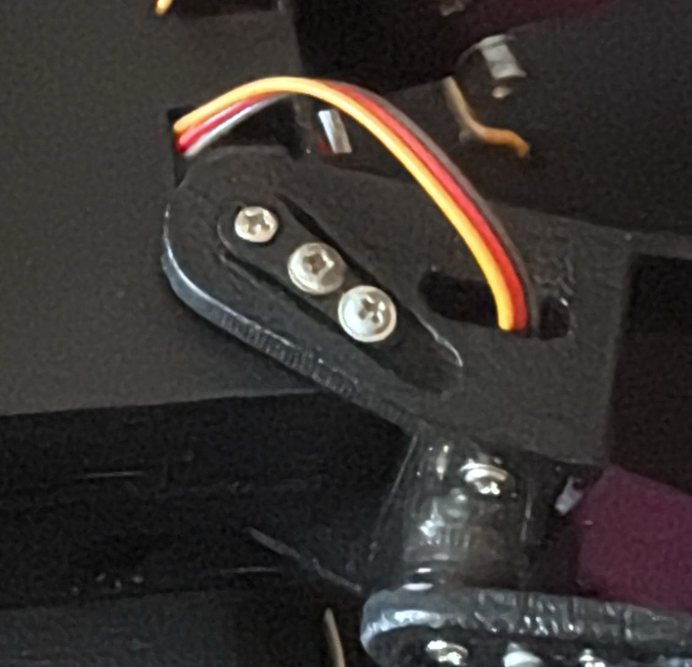
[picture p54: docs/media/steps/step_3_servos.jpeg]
  
</p>

#### 3.2. Join the elbow and the shoulder

First, identify how you should place de elbow.

<p align="center">
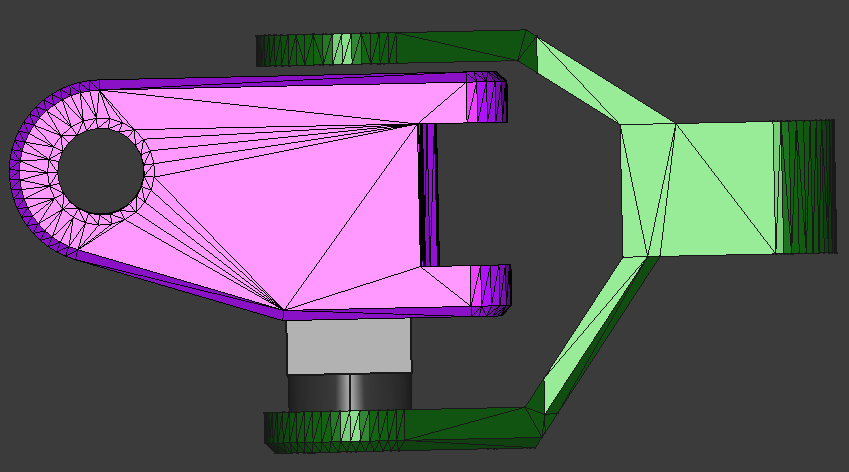
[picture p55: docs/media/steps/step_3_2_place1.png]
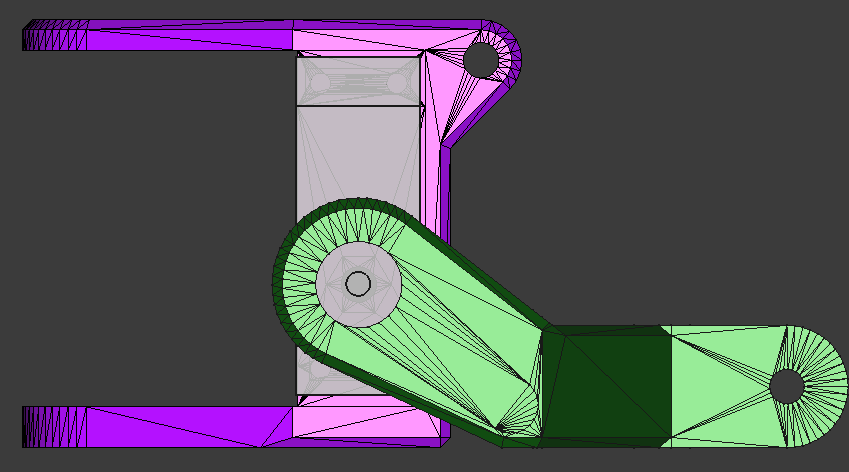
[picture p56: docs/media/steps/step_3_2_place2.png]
  
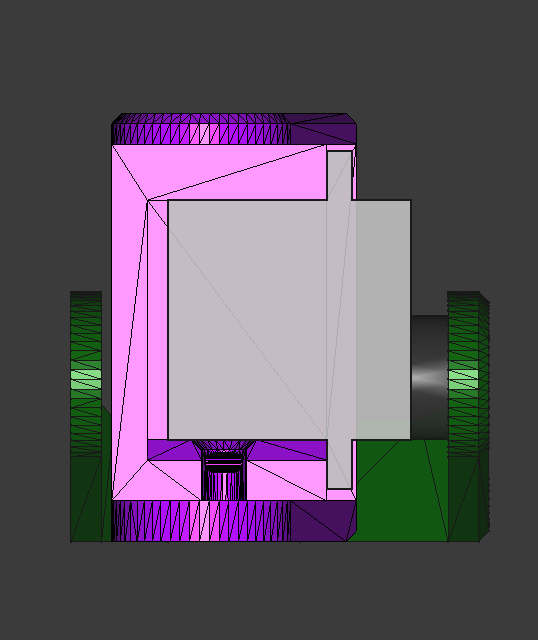
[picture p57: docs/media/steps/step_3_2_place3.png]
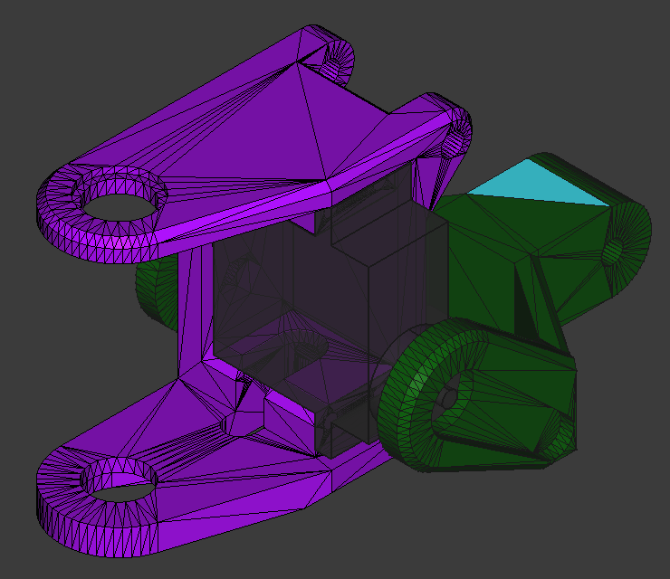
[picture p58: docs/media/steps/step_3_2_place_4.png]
  
</p>

Then, insert a `M3 nut` into the corresponding slot on the shoulder.

<p align="center">
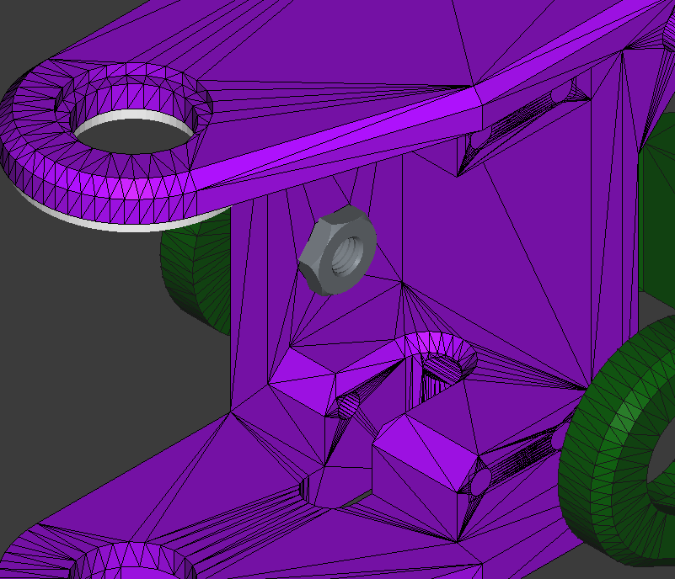
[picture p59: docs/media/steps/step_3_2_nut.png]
  
</p>

Finally, screw the elbow to the shoulder as shown, from the non-servo side.



The servo-side will be attached in [part 9](#9-assembling-legs-part-2s).

#### 3.3. Join the `leg up link` and the shoulder

Use `M3x30mm bolt` and `M3 nut`.

<p align="center">
  
</p>

### 3.4. Add the foot

Use `M3x30mm bolts` and a `M3 nuts`.

<p align="center">
  
</p>

### 3.5. Right vs Left
**REMEMBER:** *Left shoulder/elbow* are for *front left* leg and *back right* leg, while *right shoulder/elbow* are for *front right* leg and *back left* leg.

<p align="center">
  
</p>

<p align="center">
  
</p>

---
## 4. Connecting servos to `PCA9685`

Now you should connect the 8 `servos` to the `PCA9685` following the  [schematic](../electronics/brutus_schematic/brutus_electronic_schematics.svg) (<-- Click here to see it bigger):




```
      0 ---------------------------> 15
```

| Joint | `PCA9685`'s pin |
| :--- | ---: |
| Front Right Shoulder | 13 |
| Front Right Elbow | 12 |
| Front Left Shoulder | 9 |
| Front Left Elbow | 8 |
| Back Right Shoulder | 2 |
| Back Right Elbow | 3 |
| Back Left Shoulder | 0 |
| Back Left Elbow | 1 |

**Please note**, the following wires (from [part 1](#1-soldering-esp32-and-pca9685-connections)) inside the chassis must be routed out through the rear hole:
+ `ESP32` Vin or 5V
+ `ESP32` GND
+ `PCA9685` V+
+ `PCA9685` GND
+ `ESP32` GPIO 2
+ `ESP32` GPIO 15
+ `ESP32` GPIO 16
+ `ESP32` GPIO 4
+ `ESP32` GPIO 17
+ `ESP32` GPIO 5

---
### 5. Assembling chasis (Part 2)

#### 5.1. Attach the `ESP32` and the `RGB LED` to the `chasis cover`

<p align="center">
  
</p>

#### 5.2. `Chasis cover` M3 nuts

You should place 6 M3 nuts in their corresponding slots:

<p align="center">
  
</p>

#### 5.3. Join the `chasis` and the `cover`

Use a `M3x8mm bolt` at each side.

<p align="center">
  
</p>

---
### 6. Joining legs with chasis

How the legs should be placed:

<p align="center">
  
</p>

### 6.1. Leg attachment
Screw the `M3x8mm Bolt` into the nut placed in [step 5.2](#52-chasis-cover-m3-nuts1).

<p align="center">
  
</p>

---
### 7. Assembling upper box

#### 7.1. Place the `HC-SR04` sensors

<p align="center">
  
</p>

Now, place the `US sensor chasis` for each sensor:

<p align="center">
  
</p>

#### 7.2. Place the `Battery`

Before placing the battery, remove the XH2.54-2P connector from the wires and add the `switch` for turning ON and OFF the robot.

**Connector:**



**Switch connection:**

```
 ---------                          -----------
|         |---[+]------------------|           |
| Battery |                        | Connector |
|         |---[-]------------------|           |
 ---------                          -----------
```

1. Remove the connector
```
 ---------                               -----------
|         |---[+]------------------     |           |
| Battery |                             | Connector |
|         |---[-]------------------     |           |
 ---------                               -----------
```

2. Cut the wire
```
 ---------                               -----------
|         |---[+]------------------     |           |
| Battery |                             | Connector |
|         |---[-]----- ✂️ ---------     |           |
 ---------                               -----------
```

3. Add and solder the switch
```
 ---------                                   -----------
|         |---[+]----------------------     |           |
| Battery |                                 | Connector |
|         |---[-]----🧑‍🏭| Switch |🧑‍🏭----     |           |
 ---------                                   -----------
```

**Placing the `battery`**:

Then, insert the battery into the Up box, routing the wires to the upper compartment through the small slot in the corner. And then connect again the battery connector.

<p align="center">
  
</p>

Attach, using 2 `M1x5mm sheet metal screws`, the `Battery limit` to the box.

<p align="center">
  
</p>

#### 7.3. Add the `DC-DC Buck module`

First of all, cut 2 pieces of 16 AWG wire (~80 mm each), and solder them to a female XH2.54-2P.

Now, feed the wires through the back-right hole, leading them out the back.

<p align="center">
  
</p>

Now, you will solder this 2 cables to the VIN and GND terminals from the `DC-DC Buck`. To avoid a short circuit, is **ESSENTIAL** that you consider the connection of XH2.54 male (from the battery) and female (from the `DC-DC Buck`):

<p align="center">
  
</p>

<p align="center">
  
</p>

Solder the output wires (16 AWG ~110 mm each) to the `DC-DC Buck` output pins.

<p align="center">
  
</p>

Place the `DC-DC Buck` in its slot and feed the output wires through the back-right hole, leading them inside the box again. And secure the wires with a zip tie on each side.

<p align="center">
  
</p>

#### 7.4. Terminal blocks connections

Wires that will be used:
+ Vout and GND wires conected to `DC-DC Buck`
+ `ESP32` Vin or 5V (check end of [part 4](#4-connecting-servos-to-pca9685))
+ `ESP32` GND (check end of [part 4](#4-connecting-servos-to-pca9685))
+ `PCA9685` V+ (check end of [part 4](#4-connecting-servos-to-pca9685))
+ `PCA9685` GND (check end of [part 4](#4-connecting-servos-to-pca9685))
+ 6 `female-to-female jumper wires`, cut and stripped on one end.

First, loosen the two screws on each of the two `terminal blocks`.

Then, wist the exposed strands of the following wires:
+ Group (+):
  - `ESP32` Vin or 5V
  - `PCA9685` V+
  - 3 `female-to-stripped jumper wires`
+ Group (-):
  - `ESP32` GND
  - `PCA9685` GND
  - 3 `female-to-stripped jumper wires`

Now, inside the `up box`, using the `terminal blocks`, make this connections:

<p align="center">
  
</p>

Letting out of the box the *"Groups' wires"*, as shown in the image:

<p align="center">
  
</p>

#### 7.5. Connecting `HC-SR04` sensors to power supply

Connect the `HC-SR04` sensors to the power supply to the `female-to-stripped jumper wires` from the `terminal blocks`:

```
Jumper from Group (+) <---> HC-SR04 Vcc
Jumper from Group (-) <---> HC-SR04 GND
```

Use this image as reference:
<p align="center">
  
</p>

---
### 8. Joining upper box with chasis

#### 8.1. Attach `up box` to `chasis cover`

The tabs on the chassis cover are designed to fit into the slots on the bottom of the Up box. You will probably hear a 'click' when it is fully seated.

<p align="center">
  
  
</p>

#### 8.2 Connect the `HC-SR04` sensors with `ESP32`

| `HC-SR04` sensor | Trigger GPIO | Echo GPIO
| :--- | :---: | ---: |
| Frontal | 15 | 2 |
| Right | 17 | 5 |
| Left | 4 | 16 |

---
### 9. Assembling legs (Part 2)

Finally, we will attach the end of each servo to its corresponding joint.

#### 9.1. Set all servos to angle 0

We want the legs to be in approximately the same position when the 'STANDING' pose is commanded. To do this, upload the [`brutus_esp32.ino`](../src/brutus_esp32/brutus_esp32.ino) code to the robot and set it to STAND mode via the terminal or app.

#### 9.2. Attach servo's single-arm horns

With STAND mode active, position each shoulder and elbow approximately as shown in the images.

<p align="center">
  
  
</p>

Once positioned, fit the single-arm horn onto the servo, inserting the long end into the corresponding slot of the 3D-printed part. Then, using two M1x5mm sheet metal screws per servo, secure it by screwing into the nearest and furthest holes.

Now, power off the robot and use the bolt included with the servo to secure the horn to the servo's output shaft.

---

## Mechanical Maintenance

The mechanical structure of Brutus is composed of 3D-printed PLA parts, metal fasteners, bearings, and servo-mounted joints. Because the robot is constantly subjected to vibration, cyclic loads, and impacts during walking, periodic mechanical inspection is mandatory to avoid failures.

---

### Fasteners and Joint Inspection

Brutus uses the following fasteners in its structure:

- M3 bolts  
- M3 nuts  
- Sheet metal screws 
- Servo horn screws  

These elements are exposed to repeated mechanical stress during operation, especially in the legs.

The most critical areas are:
- Shoulder joints  
- Elbow joints  
- Leg link pivots  
- Foot attachments  

These joints are held together using **M3 bolts and M3 nuts inserted into the 3D-printed parts**. During normal walking, these nuts may gradually loosen and, in some cases, may even slide out of their slots if not properly tightened.

If this happens:
- The leg will develop mechanical play (backlash)
- The kinematics will become inaccurate
- The servo will be forced to compensate for the misalignment
- This leads to increased torque demand, overheating, and possible servo failure

For this reason, all leg fasteners must be inspected and tightened regularly.

---

### Bearing Condition

Each leg contains F693ZZ bearings that allow smooth rotation of the joints. These bearings must rotate freely without friction.

Signs of bearing problems:
- Grinding noise
- Increased resistance when moving a leg by hand
- Jerky or uneven motion

If a bearing becomes stiff or blocked, the servo driving that joint will operate near stall torque, which can quickly damage the servo.

---

### Servo Mounting and Horns

The MG90S servos are attached to the structure using sheet metal screws, and their horns are fixed using small M1 self-tapping screws and a central shaft screw.

These screws must be checked for:
- Looseness
- Cracks in the plastic around the holes
- Misalignment of the horn

A loose servo horn causes angular offset and loss of accuracy, which directly affects gait stability.

A malfunctioning servo can cause unstable motion, high power consumption, mechanical stress, and unpredictable behavior of the robot. The following methods allow early detection of servo problems before permanent damage occurs.

---
#### 1. Visual and Motion Inspection

While the robot is powered and standing:

- Check that all joints:
  -  Reach their commanded position
  -  Move smoothly
  -  Stop when they reach the target angle
  -  Do not overshoot or oscillate

- Warning signs:

  - One leg does not move when commanded  
  - A joint moves slower than the others 
  - The servo vibrates without changing position  
  - The servo does not return to its neutral pose
   
- This often indicates:
  - Internal gear damage  
  - Encoder failure 
  - Loss of power  
  - Mechanical binding

---

### Printed Part Inspection

All structural parts are made from PLA and are therefore subject to:
- Fatigue
- Creep
- Cracking due to cyclic load

Special attention should be paid to:
- Shoulder mounts
- Elbow parts
- Leg link interfaces
- Foot pieces

If any crack, deformation, or excessive wear is detected, the affected part must be replaced to avoid catastrophic failure during operation.

---

## Battery Maintenance and Safety

Brutus is powered by a 3S Li-ion battery. Proper handling and maintenance of the battery is critical for both safety and system reliability.

### Voltage limits
- The battery must **never be discharged below 8.0 V**.  
  Below this level, the cells may suffer irreversible damage and the BMS may permanently cut off the pack.

- The battery must **never be charged above 12.6 V**.  
  Overvoltage can cause overheating, swelling, or fire hazards.

The DC-DC buck converter will stop regulating correctly if the battery voltage falls too low, which can cause resets or erratic behavior of the ESP32 and servos.

---
### Storage recommendations
When the robot will not be used for extended periods:
- Store the battery at approximately **50–60% charge**
- Disconnect it from the robot
- Keep it in a cool, dry place

Storing the battery fully charged or fully empty for long periods significantly reduces its lifetime.

Regular battery inspection and correct charging practices are essential to ensure safe and reliable operation of Brutus.

---

### Manual Leg Check

Before powering the robot:
1. Move each leg gently by hand
2. Verify that all joints move smoothly
3. Check that there is no excessive play in the pivots
4. Confirm that no nut is missing or loose

This simple procedure prevents most mechanical failures before they occur.

---

### Electrical Connections and Wiring Integrity

All the main electrical connections of Brutus — including the ESP32, PCA9685, RGB LED and DC-DC buck converter — are permanently soldered.  
Only the ultrasonic sensors (HC-SR04) and the servos are connected using removable jumper cables.

This design minimizes contact resistance, vibration-related failures and voltage drops in high-current paths.

The power distribution of the robot follows this chain:

Battery → Switch → DC-DC Buck → Terminal Blocks → ESP32 + PCA9685 + HCSR-04 → servos + LED RGB

---
#### Critical power cables

Some cables are especially critical for safe and stable operation:

| Cable | Gauge | Function |
|---|---|---|
| Battery → DC-DC Buck | **16 AWG** | Carries the full battery current. Any fault here will instantly shut down the robot. |
| DC-DC Buck → PCA9685 (V+ and GND) | **20 AWG** | Supplies power to all servos. A bad contact will cause servo resets or brownouts. |
| DC-DC Buck → ESP32 (5V and GND) | **26 AWG** | Powers the control electronics. A bad connection causes ESP32 resets or WiFi loss. |

These cables must always be firmly soldered and mechanically strain-relieved.

---
#### Connections most likely to cause power loss

If the robot suddenly shuts down, reboots, or loses servo power, the most common causes are:

- Loose terminal block screws
- Broken solder joints on:
  - Battery wires
  - DC-DC buck input or output
  - PCA9685 power pins
- Fatigued 16 AWG battery wires near the switch or buck module

These should be inspected first before suspecting software faults.

---
#### Detecting bad contacts

A poor electrical connection typically causes one or more of the following symptoms:
- ESP32 resets when servos move
- Servos twitch or stop responding under load
- WiFi or MQTT disconnects when the robot walks
- LED flickers or changes brightness unexpectedly

To check for false contacts:
1. Power the robot ON.
2. Gently move each power cable and terminal block.
3. If the robot resets, flickers or stops, that wire has a faulty connection.
4. Re-solder or re-tighten the affected connection immediately.

---
#### Ultrasonic sensor cables

The HC-SR04 sensors are connected via removable jumper cables. These may become loose over time and should be checked periodically, especially if distance readings become unstable or incorrect.

---
## User Manual

This User Manual explains how to operate, control, and understand the internal software structure of the Brutus quadruped robot.
It is intended for users who want to run the robot, send commands, monitor its state, and modify its behavior through the ESP32 firmware and MQTT communication system.

This user manual focuses on:

- How Brutus is started and configured
- How it receives commands
- How it changes behavior between modes
- How its motion and perception systems are coordinated 
- How to control it remotely via MQTT

It also provides an overview of the main firmware components so that future users can safely extend or debug the robot without breaking its core behavior.

--- 
### Network and MQTT configuration

The file credential.h contains all the network credentials and communication parameters required for the ESP32 to connect to a WiFi network and to the MQTT broker.
This file is intentionally separated from the rest of the code in order to keep sensitive information (usernames, passwords, and network names) isolated and easy to modify without changing the main program.

This approach also allows each user to configure their own credentials without affecting the shared project code.
---
#### WiFi configuration

The system supports two different WiFi connection modes:
- **Eduroam network**, which requires a username and password instead of only an SSID and a WiFi key
- **Home / Office WiFi network**, in which only an SSID and a password are required
---
#### Network selection

In the main firmware, a configuration parameter determines whether the ESP32 should connect to the Eduroam network or to a standard WiFi network.

Depending on this parameter, the corresponding set of credentials (SSID_EDUROAM + USERNAME_EDUROAM + PASSWORD_EDUROAM, or SSID + PASSWORD) is used to establish the connection.

This design allows the same firmware to be used in different environments (university, home, office, etc.) without modifying the core program logic.

---
#### MQTT configuration

The file also defines the parameters used to connect to the MQTT broker, the values selected in the files specify the address and port of the MQTT server used for communication between the robot and external systems.

---
#### Security considerations

Since this file contains private credentials, it should not be shared publicly or uploaded to version control repositories with real data.
Each user should keep their own local copy of credential.h with their personal WiFi and Eduroam credentials.

---
#### `Credential.h` template
```cpp
#ifndef CREDENTIAL_H
#define CREDENTIAL_H

// =====================
//  WIFI - Eduroam
// =====================
#define SSID_EDUROAM     "eduroam"   // Your eduroam SSID
#define USERNAME_EDUROAM ""          // Your eduroam username
#define PASSWORD_EDUROAM ""          // Your eduroam password

// =====================
//  WIFI - Home / Office
// =====================
#define SSID     ""  // Your WiFi SSID
#define PASSWORD ""    // Your WiFi password

// =====================
//  MQTT
// =====================
#define MQTT_SERVER "test.mosquitto.org"  // Your MQTT broker address
#define MQTT_PORT   1883                 // Your MQTT broker port

#endif // CREDENTIAL_H
```
---

## `brutus_params.h` – Robot configuration and motion parameters

The file brutus_params.h contains all the global configuration parameters that define the electrical, mechanical and motion behavior of the Brutus robot.
It centralizes all tunable values so that the robot can be calibrated, adapted and modified without changing the core control logic.

This file covers:

- Servo configuration

- GPIO pin mapping

- Leg geometry and calibration

- FreeRTOS task configuration

- Motion poses and gait definitions

- Speed limits

- Perception system timing

---
### Servo configuration

```cpp
#define PWM_SERVO_FREQ 50
#define MIN_SERVO_ANGLE -90.0
#define MAX_SERVO_ANGLE 90.0
#define MIN_SERVO_PWM_PULSE_US 500
#define MAX_SERVO_PWM_PULSE_US 2500
```

These parameters define how the PWM signals are generated for the servos:

- `PWM_SERVO_FREQ` defines the PWM frequency (50 Hz), which is standard for RC servos.

- `MIN_SERVO_ANGLE` and `MAX_SERVO_ANGLE` define the angular range used by the software.

- `MIN_SERVO_PWM_PULSE_US` and `MAX_SERVO_PWM_PULSE_US` define the electrical PWM pulse width corresponding to the minimum and maximum angles.

---
### GPIO configuration

The GPIO section defines how the ESP32 is electrically connected to the sensors and actuators:
```cpp
#define US_R_TRIG 17
#define US_R_ECHO 5

#define US_L_TRIG 4
#define US_L_ECHO 16

#define US_F_TRIG 15
#define US_F_ECHO 2

#define R_PIN 32
#define G_PIN 25
#define B_PIN 33

#define PCA9685_OE 19
```

These pins correspond to:

- Three ultrasonic distance sensors (front, left and right).

- An RGB LED (R, G, B channels).

- The Output Enable (OE) pin of the PCA9685 servo controller.

---
### Leg servo mapping

Each leg has two servos:

- A shoulder (horizontal movement)

- An elbow (vertical movement)

The file defines which PCA9685 channel controls each servo:

```cpp
#define SHOULDER_BACK_LEFT_PCA_PIN 0
#define ELBOW_BACK_LEFT_PCA_PIN    1

#define SHOULDER_BACK_RIGHT_PCA_PIN 2
#define ELBOW_BACK_RIGHT_PCA_PIN    3

#define SHOULDER_FRONT_LEFT_PCA_PIN 9
#define ELBOW_FRONT_LEFT_PCA_PIN    8

#define SHOULDER_FRONT_RIGHT_PCA_PIN 13
#define ELBOW_FRONT_RIGHT_PCA_PIN    12
```

---
### Servo calibration

Mechanical assembly imperfections mean that servos are never perfectly aligned.
To compensate for this, angular offsets are defined for each joint:

```cpp
#define SHOULDER_BACK_LEFT_ANGLE_OFFSET -2.0
#define ELBOW_BACK_LEFT_ANGLE_OFFSET    -5.0

#define SHOULDER_BACK_RIGHT_ANGLE_OFFSET 3.0
#define ELBOW_BACK_RIGHT_ANGLE_OFFSET    0.0

#define SHOULDER_FRONT_LEFT_ANGLE_OFFSET -10.0
#define ELBOW_FRONT_LEFT_ANGLE_OFFSET    -12.0

#define SHOULDER_FRONT_RIGHT_ANGLE_OFFSET -2.0
#define ELBOW_FRONT_RIGHT_ANGLE_OFFSET    -20.0
```

In addition, because of the colocation of some legs, some servos are mounted in inverted orientations. This is handled by:

```cpp
#define SHOULDER_BACK_LEFT_INVERTED false
#define ELBOW_BACK_LEFT_INVERTED    true

#define SHOULDER_BACK_RIGHT_INVERTED true
#define ELBOW_BACK_RIGHT_INVERTED    false

#define SHOULDER_FRONT_LEFT_INVERTED false
#define ELBOW_FRONT_LEFT_INVERTED    false

#define SHOULDER_FRONT_RIGHT_INVERTED true
#define ELBOW_FRONT_RIGHT_INVERTED    true
```

---
### FreeRTOS task configuration

The robot software runs on FreeRTOS using two CPU cores:
```cpp
#define MOTION_CORE  0
#define LOGIC_CORE   1
```

- The motion core handles gait generation and servo control.

- The logic core handles perception, communication and high-level decision making.

Task timing is controlled by:

```cpp
#define DEFAULT_MOTION_PERIOD 300
#define MODES_PERIOD 200
```

These values define how often motion and logic tasks are executed.

---
### Pose and gait definition

The robot motion is defined using poses, represented by the `BrutusPose` structure:

```cpp
struct BrutusPose {
  BrutusLegState fr_leg_state;
  BrutusLegState fl_leg_state;
  BrutusLegState br_leg_state;
  BrutusLegState bl_leg_state;
};
```
Each pose contains the desired joint angles for the four legs.

Each pose contains the desired joint angles for the four legs.

A **gait** is defined as a sequence of poses:

```cpp
constexpr BrutusPose GAIT_STEPS[6] {GAIT_1, GAIT_2, ... , GAIT_6};
```
These poses describe a walking cycle.
A backward gait is also defined by reversing this sequence.

Spin-in-place motions are defined using the `SPIN_STEPS` arrays.

This approach makes it easy to design and tune locomotion by editing poses rather than writing complex motion equations.

---
### Speed limits

```cpp
#define MIN_W -1.0f
#define MAX_W 1.0f

#define MIN_V -1.0f
#define MAX_V 1.0f
```
These values define the allowed ranges for:

- Linear velocity (V)

- Angular velocity (W)

They are used by higher-level control to limit how fast the robot can move or turn.

---
### Perception system
```cpp
#define N_DISTANCE_SENSORS 3
#define PERCEPTION_PRIO 3
#define PERCEPTION_PERIOD 200
#define MIN_PERCEPTION_TIMEOUT 10
```

These parameters configure the ultrasonic sensor system:

- Number of sensors.

- FreeRTOS task priority.

- Update period (every 200 ms).

- Minimum allowed timeout for a measurement.

This ensures reliable obstacle detection without blocking the rest of the system.

---
## `comms_params.h` – MQTT communication configuration

The file comms_params.h centralizes all the configuration required for the robot’s communication layer.
It defines the MQTT client identity, the subscribed and published topics, timing parameters for connection handling, message buffers, and default command/data structures used at startup.

This file is designed to keep the MQTT interface consistent and easy to maintain. 

---
### MQTT client identifier

```cpp
#define CLIENT_ID "brutus_esp"
```

This is the unique MQTT client identifier used when the ESP32 connects to the broker.

---
### Subscribed topics (commands to the robot)

```cpp
#define TOPIC_CMD_MODE   "brutus/cmd/mode"
#define TOPIC_CMD_VEL    "brutus/cmd/velocity"
#define TOPIC_CMD_POSE   "brutus/cmd/pose"
```

The robot subscribes to these topics to receive commands from an external controller:

- brutus/cmd/mode: change the robot operating mode.

- brutus/cmd/velocity: set linear and angular velocity references.

- brutus/cmd/pose: directly command a full pose to the robot.

To simplify internal handling, each command is also mapped to an integer code:

```cpp
#define CMD_MODE   0
#define CMD_VEL    1
#define CMD_POSE   2
```
---
### Published topics (robot telemetry)

```cpp
#define TOPIC_STATE_HEARTBEAT "brutus/data/heartbeat"
#define TOPIC_POSE            "brutus/data/pose"
#define TOPIC_DIST_FRONT      "brutus/data/distance/front"
#define TOPIC_DIST_RIGHT      "brutus/data/distance/right"
#define TOPIC_DIST_LEFT       "brutus/data/distance/left"
```

The robot publishes telemetry data to these topics:

- `brutus/data/heartbeat`: periodic status message that indicates the robot is alive and connected.

- `brutus/data/pose`: the pose currently executed by the robot.

- `brutus/data/distance/*`: distances measured by the ultrasonic sensors (front, right, left).

Similarly, message types are mapped to integer identifiers:

```cpp
#define STATE_HEARTBEAT 0
#define POSE            1
#define DIST_FRONT      2
#define DIST_RIGHT      3
#define DIST_LEFT       4
```
---
### Connection timing parameters

```cpp
#define WIFI_WAIT 500
#define RECONNECT_WAIT 3000
```

- `WIFI_WAIT` sets the delay (in milliseconds) used while waiting for WiFi to connect.

- `RECONNECT_WAIT` sets the delay (in milliseconds) between MQTT reconnection attempts if the connection is lost.

These values avoid aggressive reconnection loops and help keep the system stable.

---
### Network mode selection (Eduroam vs normal WiFi)

```cpp
#define IS_EDUROAM false
```

This parameter selects which WiFi credentials should be used during initialization:

- true: connect using ***Eduroam*** credentials (enterprise authentication).

- false: connect using a ***standard WiFi network*** (SSID + password).

The actual credentials are defined in credential.h, while this flag determines which set of credentials will be used by the connection code.

---
### Ranges for test/debug messages

```cpp
#define MIN_LEG_DEG 0
#define MAX_LEG_DEG 181
#define MIN_DIST 0
#define MAX_DIST 200
```

These ranges are created in order to put a limit to the leg degrees and the distance the ultrasonic sensor can reach.

---
### Joint identifier strings

```cpp
#define SHOULDER "0"
#define ELBOW "1"
```

These string identifiers are used in message payloads (JSON fields) to label which joint is being referenced.

---
### Buffers and message sizes

```cpp
#define MSG_BUFFER 254
#define JSON_BUFFER 300
```

These values define the maximum sizes used to store incoming/outgoing MQTT payloads:

- `MSG_BUFFER`: raw MQTT message buffer length.

- `JSON_BUFFER`: buffer size for JSON serialization/deserialization.

---
### Task timing and serial configuration

```cpp
#define COMMS_PERIOD 200
#define COMMS_CORE LOGIC_CORE
#define BAUD 115200
```

- `COMMS_PERIOD` defines how often the communications task runs (every 200 ms).

- `COMMS_CORE` pins the task to the logic core (LOGIC_CORE), keeping communications separate from real-time motion control.

- `BAUD` sets the serial debugging baud rate.

---
### Default startup command and telemetry

```cpp
constexpr BrutusCommsCmd START_CMD {0, 0.0, 0.0, STANDING_POSE};
constexpr BrutusCommsData START_DATA {STANDING_POSE, 0.0, 0.0, 0.0};
```

At startup, the robot initializes both the current command and telemetry structures with safe default values:

- START_CMD initializes:

  - mode = 0 (default mode)

  - linear velocity v = 0.0

  - angular velocity w = 0.0

  - pose = STANDING_POSE

- START_DATA initializes:

  - pose = STANDING_POSE

  - ultrasonic distances set to 0.0 until valid measurements are available.

---

## User Sketch
### Enum Declaration

This enum is declared to be used in the state machine created in the logic task.
```c
enum FuncMode {
  STANDING = 0,
  EXERCISE_1 = 1,
  EXERCISE_2 = 2,
  LEG_CONTROL = 3,
  VEL_CONTROL = 4
};
```
---
### Variable Declaration

In this section, the main system objects are declared.  
The **PCA (`Adafruit_PWMServoDriver`)** is not only declared but also **initialized to enable control of the different servos**.  
Additionally, the `brutus_comms` object is declared, which is responsible for communications, and the `brutus` object, which handles both motion control and sensory processing.  
Finally, the *task handle* that manages the system logic is declared.

```c
Adafruit_PWMServoDriver pca = Adafruit_PWMServoDriver();

Brutus brutus;
BrutusComms brutus_comms;

TaskHandle_t mode_task_handle;
```
---
### Setup()
#### Brutus
First, Brutus is prepared for operation by calling the general setup function. In this step, the PCA controller, the LED pins, and the PWM frequency used for servo control are assigned.

Next, the setup functions for each of Brutus’ legs are called individually. In each call, the PCA pins to which the two servos of each leg (shoulder and elbow) are connected are specified, along with the minimum and maximum PWM values and the angular limits for each servomotor. Angular offsets are also defined to compensate for possible mechanical inaccuracies caused by imperfect physical calibration. Due to the physical arrangement of the legs, some servos require inversion of the rotation direction to ensure correct movement; this behavior is configured using the last two parameters of each function.

Then, the perception system is initialized, which includes the ultrasonic sensors. Once all configuration steps are completed, the function brutus.start() is called, leaving the system fully ready for use.

After this initialization, it is possible to set the robot’s desired initial configuration. The code provides an example of a possible initial setup.

Finally, the task that will manage both movement and perception is created

```c
brutus.setup(&pca,
               PCA9685_OE,
               R_PIN,
               B_PIN,
               G_PIN,
               PWM_SERVO_FREQ);

brutus.setup_front_right_leg(SHOULDER_FRONT_RIGHT_PCA_PIN, ELBOW_FRONT_RIGHT_PCA_PIN,
                            MIN_SERVO_PWM_PULSE_US, MAX_SERVO_PWM_PULSE_US,
                            MIN_SERVO_PWM_PULSE_US, MAX_SERVO_PWM_PULSE_US,
                            MIN_SERVO_ANGLE, MAX_SERVO_ANGLE,
                            MIN_SERVO_ANGLE, MAX_SERVO_ANGLE,
                            SHOULDER_FRONT_RIGHT_ANGLE_OFFSET, ELBOW_FRONT_RIGHT_ANGLE_OFFSET,
                            SHOULDER_FRONT_RIGHT_INVERTED, ELBOW_FRONT_RIGHT_INVERTED);

brutus.setup_front_left_leg(SHOULDER_FRONT_LEFT_PCA_PIN,    ELBOW_FRONT_LEFT_PCA_PIN,
                            MIN_SERVO_PWM_PULSE_US, MAX_SERVO_PWM_PULSE_US,
                            MIN_SERVO_PWM_PULSE_US, MAX_SERVO_PWM_PULSE_US,
                            MIN_SERVO_ANGLE, MAX_SERVO_ANGLE,
                            MIN_SERVO_ANGLE, MAX_SERVO_ANGLE,
                            SHOULDER_FRONT_LEFT_ANGLE_OFFSET, ELBOW_FRONT_LEFT_ANGLE_OFFSET,
                            SHOULDER_FRONT_LEFT_INVERTED, ELBOW_FRONT_LEFT_INVERTED);

brutus.setup_back_right_leg(SHOULDER_BACK_RIGHT_PCA_PIN, ELBOW_BACK_RIGHT_PCA_PIN,
                            MIN_SERVO_PWM_PULSE_US, MAX_SERVO_PWM_PULSE_US,
                            MIN_SERVO_PWM_PULSE_US, MAX_SERVO_PWM_PULSE_US,
                            MIN_SERVO_ANGLE, MAX_SERVO_ANGLE,
                            MIN_SERVO_ANGLE, MAX_SERVO_ANGLE,
                            SHOULDER_BACK_RIGHT_ANGLE_OFFSET, ELBOW_BACK_RIGHT_ANGLE_OFFSET,
                            SHOULDER_BACK_RIGHT_INVERTED, ELBOW_BACK_RIGHT_INVERTED);

brutus.setup_back_left_leg(SHOULDER_BACK_LEFT_PCA_PIN, ELBOW_BACK_LEFT_PCA_PIN,
                            MIN_SERVO_PWM_PULSE_US, MAX_SERVO_PWM_PULSE_US,
                            MIN_SERVO_PWM_PULSE_US, MAX_SERVO_PWM_PULSE_US,
                            MIN_SERVO_ANGLE, MAX_SERVO_ANGLE,
                            MIN_SERVO_ANGLE, MAX_SERVO_ANGLE,
                            SHOULDER_BACK_LEFT_ANGLE_OFFSET, ELBOW_BACK_LEFT_ANGLE_OFFSET,
                            SHOULDER_BACK_LEFT_INVERTED, ELBOW_BACK_LEFT_INVERTED);

brutus.setup_perception(US_R_TRIG,
                        US_R_ECHO,
                        US_L_TRIG,
                        US_L_ECHO,
                        US_F_TRIG,
                        US_F_ECHO,
                        MIN_PERCEPTION_TIMEOUT);

brutus.start();

brutus.set_linear_speed_ts(0.0);
brutus.set_angular_speed_ts(0.0);
brutus.change_target_pose(STANDING_POSE);

brutus.set_motion_control_mode(POSE_CONTROL);

brutus.create_motion_task(DEFAULT_MOTION_PERIOD, MOTION_CORE);
brutus.create_perception_task(PERCEPTION_PERIOD, LOGIC_CORE, PERCEPTION_PRIO);
```
---
#### Brutus Comms
To initialize BrutusComms, simply call the start function first, and then create the task that will manage communications.

```c
brutus_comms.start(&brutus);
brutus_comms.create_comms_task(COMMS_CORE); 

```

---
#### Logic Task
Finally, we create the task that will manage Brutus’ highest-level logic, that is, what to do in each mode.
```c
  xTaskCreatePinnedToCore(
    (TaskFunction_t)mode_task,
    "ModeTask",
    MODES_TASK_SIZE,
    NULL,
    2,
    &mode_task_handle,
    LOGIC_CORE
  );
```

---

## Logic Task Definition
It is worth noting that in each mode we change the eye color to indicate the current mode, although this is not strictly necessary.

```c
void
mode_task(void* pvParameters)
{
  BrutusCommsCmd cmd;
  
  // Initial values
  enum FuncMode mode = EXERCISE_1;
  enum FuncMode last_mode = STANDING;

  BrutusPose pose = brutus.check_pose(true);

  float fr_elbow = 0.0;
  float fl_elbow = 0.0;
  float br_elbow = 0.0;
  float bl_elbow = 0.0;

  while (true) {
    // We update the command using the information received through MQTT
    cmd = brutus_comms.getCmd();
    mode = FuncMode(cmd.mode);

    switch (mode)
    {
      case STANDING:
        if (mode != last_mode) {
          brutus.eyes_blue();
          // We set Brutus to operate in pose control mode.
          brutus.set_motion_control_mode(POSE_CONTROL);
          last_mode = mode;
        }
        // Set brutus to STANDING_POSE
        brutus.change_target_pose(STANDING_POSE);
        break;
      
      case LEG_CONTROL:
        if (mode != last_mode) {
          brutus.eyes_yellow();
          // We set Brutus to operate in pose control mode.
          brutus.set_motion_control_mode(POSE_CONTROL);
          last_mode = mode;
        }

        brutus.change_target_pose(interp_pose_norm(cmd.pose));
        break;

      case VEL_CONTROL:
        if (mode != last_mode) {
          brutus.eyes_green();
          // We set Brutus to operate in speed control mode.
          brutus.set_motion_control_mode(SPEED_CONTROL);
          last_mode = mode;
        }

        // We use the v and w recived from comms to set Brutus v and w
        brutus.set_linear_speed_ts(cmd.v);
        brutus.set_angular_speed_ts(cmd.w);
        break;

      case EXERCISE_1:
        // Logic of exercise 1
        continue;
        break;

      case EXERCISE_2:
        // Logic of exercise 2
        continue;
        break;

      default:
        break;
    }
  }
}
```
---

## Doxygen

If you want to look for more information about the classes, structs and methods from our project, please checkout [this link](https://sons-of-brutus.github.io/Robot_Brutus/).

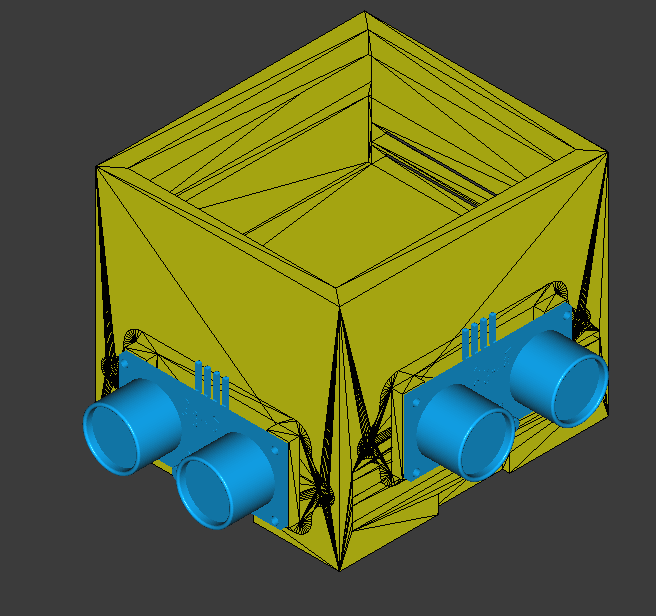
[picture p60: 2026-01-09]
docs/media/steps/step_7_1_1_rf.png

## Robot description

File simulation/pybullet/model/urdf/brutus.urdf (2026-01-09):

<robot name="brutus" version="1.0">
  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
  <joint name="chasis_to_cover" type="fixed">
    <parent link="base_link"/>
    <child link="chasis_cover_link"/>
    <origin rpy="0 0 0" xyz="0.0 0.0 0.0208"/>
  </joint>
  <joint name="cover_to_fr_spacer" type="fixed">
    <parent link="chasis_cover_link"/>
    <child link="spacer_fr"/>
    <origin rpy="0 0 0" xyz="0.023 0.023 0.0015"/>
  </joint>
  <joint name="cover_to_fl_spacer" type="fixed">
    <parent link="chasis_cover_link"/>
    <child link="spacer_fl"/>
    <origin rpy="0 0 0" xyz="-0.023 0.023 0.0015"/>
  </joint>
  <joint name="cover_to_br_spacer" type="fixed">
    <parent link="chasis_cover_link"/>
    <child link="spacer_br"/>
    <origin rpy="0 0 0" xyz="0.023 -0.023 0.0015"/>
  </joint>
  <joint name="cover_to_bl_spacer" type="fixed">
    <parent link="chasis_cover_link"/>
    <child link="spacer_bl"/>
    <origin rpy="0 0 0" xyz="-0.023 -0.023 0.0015"/>
  </joint>
  <joint name="00_spacer_to_leg_elbow_br" type="revolute">
    <parent link="spacer_br"/>
    <child link="leg_elbow_br"/>
    <origin rpy="0 0 0" xyz="0.0 0.0 -0.0175"/>
    <axis xyz="0 0 1"/>
    <limit effort="0.17" lower="-1.0471975511965976" upper="1.0471975511965976" velocity="10.471975511965978"/>
  </joint>
  <joint name="10_spacer_to_leg_elbow_bl" type="revolute">
    <parent link="spacer_bl"/>
    <child link="leg_elbow_bl"/>
    <origin rpy="0 0 0" xyz="0.0 0.0 -0.0175"/>
    <axis xyz="0 0 1"/>
    <limit effort="0.17" lower="-1.0471975511965976" upper="1.0471975511965976" velocity="10.471975511965978"/>
  </joint>
  <joint name="20_spacer_to_leg_elbow_fl" type="revolute">
    <parent link="spacer_fl"/>
    <child link="leg_elbow_fl"/>
    <origin rpy="0 0 0" xyz="0.0 0.0 -0.0175"/>
    <axis xyz="0 0 1"/>
    <limit effort="0.17" lower="-1.0471975511965976" upper="1.0471975511965976" velocity="10.471975511965978"/>
  </joint>
  <joint name="30_spacer_to_leg_elbow_fr" type="revolute">
    <parent link="spacer_fr"/>
    <child link="leg_elbow_fr"/>
    <origin rpy="0 0 0" xyz="0.0 0.0 -0.0175"/>
    <axis xyz="0 0 1"/>
    <limit effort="0.17" lower="-1.0471975511965976" upper="1.0471975511965976" velocity="10.471975511965978"/>
  </joint>
  <joint name="leg_elbow_to_leg_upper_axis_br" type="fixed">
    <parent link="leg_elbow_br"/>
    <child link="leg_upper_axis_br"/>
    <origin rpy="-1.5707963267948968 0 3.141592653589793" xyz="0.036 0.009 0.017"/>
  </joint>
  <joint name="leg_upper_axis_to_upper_link_br" type="fixed">
    <parent link="leg_upper_axis_br"/>
    <child link="upper_link_br"/>
    <origin rpy="0 0 0" xyz="0.0 0.0 0.01197"/>
  </joint>
  <joint name="leg_elbow_to_leg_upper_axis_bl" type="fixed">
    <parent link="leg_elbow_bl"/>
    <child link="leg_upper_axis_bl"/>
    <origin rpy="-1.5707963267948968 0 0" xyz="-0.036 -0.015 0.017"/>
  </joint>
  <joint name="leg_upper_axis_to_upper_link_bl" type="fixed">
    <parent link="leg_upper_axis_bl"/>
    <child link="upper_link_bl"/>
    <origin rpy="0 0 0" xyz="0.0 0.0 0.01197"/>
  </joint>
  <joint name="leg_upper_axis_to_upper_link_fl" type="fixed">
    <parent link="leg_upper_axis_fl"/>
    <child link="upper_link_fl"/>
    <origin rpy="0 0 0" xyz="0.0 0.0 0.01197"/>
  </joint>
  <joint name="leg_elbow_to_leg_upper_axis_fl" type="fixed">
    <parent link="leg_elbow_fl"/>
    <child link="leg_upper_axis_fl"/>
    <origin rpy="-1.5707963267948963 0 0" xyz="-0.036 -0.009 0.017"/>
  </joint>
  <joint name="leg_elbow_to_leg_upper_axis_fr" type="fixed">
    <parent link="leg_elbow_fr"/>
    <child link="leg_upper_axis_fr"/>
    <origin rpy="-1.5707963267948968 0 3.141592653589793" xyz="0.036 0.015 0.017"/>
  </joint>
  <joint name="leg_upper_axis_to_upper_link_fr" type="fixed">
    <parent link="leg_upper_axis_fr"/>
    <child link="upper_link_fr"/>
    <origin rpy="0 0 0" xyz="0.0 0.0 0.01197"/>
  </joint>
  <joint name="leg_elbow_to_leg_bottom_axis_br" type="fixed">
    <parent link="leg_elbow_br"/>
    <child link="leg_bottom_axis_br"/>
    <origin rpy="1.5707963267948963 0 0" xyz="0.02425 0.0 -0.0049"/>
  </joint>
  <joint name="leg_elbow_to_leg_bottom_axis_fl" type="fixed">
    <parent link="leg_elbow_fl"/>
    <child link="leg_bottom_axis_fl"/>
    <origin rpy="1.5707963267948968 0 3.141592653589793" xyz="-0.024 0.0 -0.0049"/>
  </joint>
  <joint name="01_leg_bottom_axis_to_leg_bottom_link_br" type="revolute">
    <parent link="leg_bottom_axis_br"/>
    <child link="leg_bottom_link_br"/>
    <origin rpy="0 0 0" xyz="0.0 0.0 0.0261"/>
    <axis xyz="0 0 1"/>
    <limit effort="0.17" lower="-1.0471975511965976" upper="1.0471975511965976" velocity="10.471975511965978"/>
  </joint>
  <joint name="21_leg_bottom_axis_to_leg_bottom_link_fl" type="revolute">
    <parent link="leg_bottom_axis_fl"/>
    <child link="leg_bottom_link_fl"/>
    <origin rpy="0 0 0" xyz="0.0 0.0 0.0261"/>
    <axis xyz="0 0 1"/>
    <limit effort="0.17" lower="-1.0471975511965976" upper="1.0471975511965976" velocity="10.471975511965978"/>
  </joint>
  <joint name="11_leg_bottom_axis_to_leg_bottom_link_bl" type="revolute">
    <parent link="leg_bottom_axis_bl"/>
    <child link="leg_bottom_link_bl"/>
    <origin rpy="0 0 0" xyz="0.0 0.0 0.0261"/>
    <axis xyz="0 0 1"/>
    <limit effort="0.17" lower="-1.0471975511965976" upper="1.0471975511965976" velocity="10.471975511965978"/>
  </joint>
  <joint name="leg_elbow_to_leg_bottom_axis_bl" type="fixed">
    <parent link="leg_elbow_bl"/>
    <child link="leg_bottom_axis_bl"/>
    <origin rpy="1.5707963267948963 0 0" xyz="-0.024 0.0 -0.0049"/>
  </joint>
  <joint name="leg_elbow_to_leg_bottom_axis_fr" type="fixed">
    <parent link="leg_elbow_fr"/>
    <child link="leg_bottom_axis_fr"/>
    <origin rpy="1.5707963267948968 0 -3.141592653589793" xyz="0.024 0.0 -0.0049"/>
  </joint>
  <joint name="31_leg_bottom_axis_to_leg_bottom_link_fr" type="revolute">
    <parent link="leg_bottom_axis_fr"/>
    <child link="leg_bottom_link_fr"/>
    <origin rpy="0 0 0" xyz="0.0 0.0 0.0261"/>
    <axis xyz="0 0 1"/>
    <limit effort="0.17" lower="-1.0471975511965976" upper="1.0471975511965976" velocity="10.471975511965978"/>
  </joint>
  <joint name="leg_bottom_link_to_foot_axis_fr" type="fixed">
    <parent link="leg_bottom_link_fr"/>
    <child link="foot_axis_fr"/>
    <origin rpy="0 0 0" xyz="-0.042 -0.01 -0.02935"/>
  </joint>
  <joint name="32_foot_axis_to_foot_link_fr" type="revolute">
    <parent link="foot_axis_fr"/>
    <child link="foot_link_fr"/>
    <origin rpy="0 0 0" xyz="0.0 0.0 0.0065"/>
    <axis xyz="0 0 1"/>
    <limit effort="-0.17" lower="-1.0471975511965976" upper="1.0471975511965976" velocity="10.471975511965978"/>
  </joint>
  <joint name="leg_bottom_link_to_foot_axis_br" type="fixed">
    <parent link="leg_bottom_link_br"/>
    <child link="foot_axis_br"/>
    <origin rpy="3.141592653589793 0 3.141592653589793" xyz="0.042 -0.01 -0.02935"/>
  </joint>
  <joint name="02_foot_axis_to_foot_link_br" type="revolute">
    <parent link="foot_axis_br"/>
    <child link="foot_link_br"/>
    <origin rpy="0 0 0" xyz="0.0 0.0 -0.0065"/>
    <axis xyz="0 0 1"/>
    <limit effort="0.17" lower="-1.0471975511965976" upper="1.0471975511965976" velocity="10.471975511965978"/>
  </joint>
  <joint name="leg_bottom_link_to_foot_axis_fl" type="fixed">
    <parent link="leg_bottom_link_fl"/>
    <child link="foot_axis_fl"/>
    <origin rpy="3.141592653589793 0 3.141592653589793" xyz="0.042 -0.01 -0.01635"/>
  </joint>
  <joint name="22_foot_axis_to_foot_link_fl" type="revolute">
    <parent link="foot_axis_fl"/>
    <child link="foot_link_fl"/>
    <origin rpy="0 0 0" xyz="0.0 0.0 0.0065"/>
    <axis xyz="0 0 1"/>
    <limit effort="0.17" lower="-1.0471975511965976" upper="1.0471975511965976" velocity="10.471975511965978"/>
  </joint>
  <joint name="leg_bottom_link_to_foot_axis_bl" type="fixed">
    <parent link="leg_bottom_link_bl"/>
    <child link="foot_axis_bl"/>
    <origin rpy="0 0 0" xyz="-0.042 -0.01 -0.02935"/>
  </joint>
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

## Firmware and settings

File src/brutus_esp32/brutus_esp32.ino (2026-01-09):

#include "Brutus.h"
#include "BrutusComms.h"

//EX1

#define W_EX1 0.45
#define V_EX1 1
#define NEAREST_DIST 13
#define FURTHER_DIST 16.0

#define INITIAL_SAMPLES 3
// STATES
#define PREPARE 0
#define START 1
#define FINISH 2

enum FuncMode {
  STANDING = 0,
  EXERCISE_1 = 1,
  EXERCISE_2 = 2,
  LEG_CONTROL = 3,
  VEL_CONTROL = 4
};

Adafruit_PWMServoDriver pca = Adafruit_PWMServoDriver();

Brutus brutus;
BrutusComms brutus_comms;

TaskHandle_t mode_task_handle;

bool start_tasks = false;

void setup() {
  Serial.begin(BAUD);

  brutus.setup(&pca,
               PCA9685_OE,
               R_PIN,
               B_PIN,
               G_PIN,
               PWM_SERVO_FREQ);

  brutus.setup_front_right_leg(SHOULDER_FRONT_RIGHT_PCA_PIN, ELBOW_FRONT_RIGHT_PCA_PIN,
                              MIN_SERVO_PWM_PULSE_US, MAX_SERVO_PWM_PULSE_US,
                              MIN_SERVO_PWM_PULSE_US, MAX_SERVO_PWM_PULSE_US,
                              MIN_SERVO_ANGLE, MAX_SERVO_ANGLE,
                              MIN_SERVO_ANGLE, MAX_SERVO_ANGLE,
                              SHOULDER_FRONT_RIGHT_ANGLE_OFFSET, ELBOW_FRONT_RIGHT_ANGLE_OFFSET,
                              SHOULDER_FRONT_RIGHT_INVERTED, ELBOW_FRONT_RIGHT_INVERTED);

  brutus.setup_front_left_leg(SHOULDER_FRONT_LEFT_PCA_PIN, ELBOW_FRONT_LEFT_PCA_PIN,
                              MIN_SERVO_PWM_PULSE_US, MAX_SERVO_PWM_PULSE_US,
                              MIN_SERVO_PWM_PULSE_US, MAX_SERVO_PWM_PULSE_US,
                              MIN_SERVO_ANGLE, MAX_SERVO_ANGLE,
                              MIN_SERVO_ANGLE, MAX_SERVO_ANGLE,
                              SHOULDER_FRONT_LEFT_ANGLE_OFFSET, ELBOW_FRONT_LEFT_ANGLE_OFFSET,
                              SHOULDER_FRONT_LEFT_INVERTED, ELBOW_FRONT_LEFT_INVERTED);

  brutus.setup_back_right_leg(SHOULDER_BACK_RIGHT_PCA_PIN, ELBOW_BACK_RIGHT_PCA_PIN,
                              MIN_SERVO_PWM_PULSE_US, MAX_SERVO_PWM_PULSE_US,
                              MIN_SERVO_PWM_PULSE_US, MAX_SERVO_PWM_PULSE_US,
                              MIN_SERVO_ANGLE, MAX_SERVO_ANGLE,
                              MIN_SERVO_ANGLE, MAX_SERVO_ANGLE,
                              SHOULDER_BACK_RIGHT_ANGLE_OFFSET, ELBOW_BACK_RIGHT_ANGLE_OFFSET,
                              SHOULDER_BACK_RIGHT_INVERTED, ELBOW_BACK_RIGHT_INVERTED);

  brutus.setup_back_left_leg(SHOULDER_BACK_LEFT_PCA_PIN, ELBOW_BACK_LEFT_PCA_PIN,
                             MIN_SERVO_PWM_PULSE_US, MAX_SERVO_PWM_PULSE_US,
                             MIN_SERVO_PWM_PULSE_US, MAX_SERVO_PWM_PULSE_US,
                             MIN_SERVO_ANGLE, MAX_SERVO_ANGLE,
                             MIN_SERVO_ANGLE, MAX_SERVO_ANGLE,
                             SHOULDER_BACK_LEFT_ANGLE_OFFSET, ELBOW_BACK_LEFT_ANGLE_OFFSET,
                             SHOULDER_BACK_LEFT_INVERTED, ELBOW_BACK_LEFT_INVERTED);

  brutus.setup_perception(US_R_TRIG,
                          US_R_ECHO,
                          US_L_TRIG,
                          US_L_ECHO,
                          US_F_TRIG,
                          US_F_ECHO,
                          MIN_PERCEPTION_TIMEOUT);

  delay(3000);

  brutus_comms.start(&brutus);
  brutus.start();
  delay(100);

  //Serial.println("<START>");
  
  brutus.set_linear_speed_ts(0.0);
  brutus.set_angular_speed_ts(0.0);
  brutus.change_target_pose(STANDING_POSE);

  brutus.set_motion_control_mode(POSE_CONTROL);
  
  brutus.create_motion_task(DEFAULT_MOTION_PERIOD, MOTION_CORE);
  brutus.create_perception_task(PERCEPTION_PERIOD, LOGIC_CORE, PERCEPTION_PRIO);
  
  xTaskCreatePinnedToCore(
    (TaskFunction_t)mode_task,
    "ModeTask",
    MODES_TASK_SIZE,
    NULL,
    2,
    &mode_task_handle,
    LOGIC_CORE
  );

  brutus_comms.create_comms_task(COMMS_CORE); 
}

void loop() {}

void
mode_task(void* pvParameters)
{
  enum FuncMode mode = EXERCISE_1;
  enum FuncMode last_mode = STANDING;
  BrutusCommsCmd cmd;

  BrutusPerception perception_data;

  TickType_t last_wake_time = xTaskGetTickCount();
  

  BrutusPose pose = brutus.check_pose(true);

  float fr_elbow = 0.0;
  float fl_elbow = 0.0;
  float br_elbow = 0.0;
  float bl_elbow = 0.0;

  BrutusPose dbg_pose;

  float w = 0.0;

  float dist;

  bool is_right;
  int state_ex1 = PREPARE;
  int sign;
  int samples_taken = 0;
  float dists_right[INITIAL_SAMPLES];
  float dists_left[INITIAL_SAMPLES];
  float med_right_dist = 0;
  float med_left_dist = 0;
  while (true) {
    uint32_t start_time = micros();

    cmd = brutus_comms.getCmd();
    mode = FuncMode(cmd.mode);

    switch (mode)
    {
      case STANDING:
        if (mode != last_mode) {
          brutus.eyes_blue();
          brutus.set_motion_control_mode(POSE_CONTROL);
          last_mode = mode;
          state_ex1 = PREPARE;
        }

        brutus.change_target_pose(STANDING_POSE);
        break;
      
      case LEG_CONTROL:
        if (mode != last_mode) {
          brutus.eyes_yellow();
          brutus.set_motion_control_mode(POSE_CONTROL);
          last_mode = mode;
          state_ex1 = PREPARE;
        }

        brutus.change_target_pose(interp_pose_norm(cmd.pose));
        break;

      case VEL_CONTROL:
        if (mode != last_mode) {
          brutus.eyes_green();
          brutus.set_motion_control_mode(SPEED_CONTROL);
          last_mode = mode;
          state_ex1 = PREPARE;
        }

        brutus.set_linear_speed_ts(cmd.v);
        brutus.set_angular_speed_ts(cmd.w);
        break;

      case EXERCISE_1:
        switch(state_ex1) {
          case PREPARE:
            if (mode != last_mode) {
              brutus.eyes_white();
              brutus.set_motion_control_mode(SPEED_CONTROL);
              last_mode = mode;
            }
            brutus.set_linear_speed_ts(V_EX1);

            perception_data = brutus.get_perception_data();

            dists_right[samples_taken] = perception_data.right_dist;
            dists_left[samples_taken] = perception_data.left_dist;

            if(is_right) {
              sign = 1;
            } else {
              sign = -1;
            }

            if (samples_taken >= INITIAL_SAMPLES) {
              med_right_dist = median(dists_right, INITIAL_SAMPLES);
              med_left_dist = median(dists_left, INITIAL_SAMPLES);

              is_right = (med_right_dist < med_left_dist);

              if(is_right) {
                sign = 1;
              } else {
                sign = -1;
              }
              samples_taken = 0;
              state_ex1 = START;
            } else {
              samples_taken++;
            }
            break;
          case START:
          perception_data = brutus.get_perception_data();
          if(is_right) {
              dist = perception_data.right_dist;
            } else {
              dist = perception_data.left_dist;
            }

            if (dist < NEAREST_DIST) {
              brutus.eyes_blue();
              brutus.set_angular_speed_ts(-W_EX1 * sign);
            } else if (dist > FURTHER_DIST) {
              brutus.eyes_red();
              brutus.set_angular_speed_ts(W_EX1 * sign);
            } else {
              brutus.eyes_magenta();
              brutus.set_angular_speed_ts(0);
            }

            if (perception_data.front_dist < FRONT_LIMIT_CM) {
              brutus.set_linear_speed_ts(0.0);
              brutus.set_angular_speed_ts(0.0);
              brutus.eyes_yellow();
            }
            brutus_comms.set_debug_float(dist);
          break;
        }
        break;

      case EXERCISE_2:
        if (mode != last_mode) {
          state_ex1 = PREPARE;
          brutus.eyes_magenta();
          brutus.set_motion_control_mode(SPEED_CONTROL);
          last_mode = mode;
        }

        break;

      default:
        break;
    }

    uint32_t end_time = micros();
    uint32_t execution_time_us = end_time - start_time;

    vTaskDelayUntil(&last_wake_time, pdMS_TO_TICKS(MODES_PERIOD));
  }
}

float
calc_slope(float *values, int n_values)
{
  float sumX = 0, sumY = 0, sumXY = 0, sumX2 = 0;

  for (int i = 0; i < n_values; i++) {
    float x = i;
    sumX += x;
    sumY += values[i];
    sumXY += x * values[i];
    sumX2 += x * x;
  }

  float numerador = (n_values * sumXY) - (sumX * sumY);
  float denominador = (n_values * sumX2) - (sumX * sumX);
  
  return numerador / denominador;
}

float mapf_constrained(float x, float in_min, float in_max,
                       float out_min, float out_max)
{
    if (x < in_min) x = in_min;
    if (x > in_max) x = in_max;

    return (x - in_min) * (out_max - out_min) / (in_max - in_min) + out_min;
}

BrutusPose interp_pose_norm(const BrutusPose& norm_pose)
{
  BrutusPose out;

  out.fr_leg_state.shoulder_angle = mapf_constrained(norm_pose.fr_leg_state.shoulder_angle, -1.0, 1.0,
                                                     MIN_SERVO_ANGLE, MAX_SERVO_ANGLE);
  out.fr_leg_state.elbow_angle    = mapf_constrained(norm_pose.fr_leg_state.elbow_angle, -1.0, 1.0,
                                                     MIN_SERVO_ANGLE, MAX_SERVO_ANGLE);

  out.fl_leg_state.shoulder_angle = mapf_constrained(norm_pose.fl_leg_state.shoulder_angle, -1.0, 1.0,
                                                     MIN_SERVO_ANGLE, MAX_SERVO_ANGLE);
  out.fl_leg_state.elbow_angle    = mapf_constrained(norm_pose.fl_leg_state.elbow_angle, -1.0, 1.0,
                                                     MIN_SERVO_ANGLE, MAX_SERVO_ANGLE);

  out.br_leg_state.shoulder_angle = mapf_constrained(norm_pose.br_leg_state.shoulder_angle, -1.0, 1.0,
                                                     MIN_SERVO_ANGLE, MAX_SERVO_ANGLE);
  out.br_leg_state.elbow_angle    = mapf_constrained(norm_pose.br_leg_state.elbow_angle, -1.0, 1.0,
                                                     MIN_SERVO_ANGLE, MAX_SERVO_ANGLE);

  out.bl_leg_state.shoulder_angle = mapf_constrained(norm_pose.bl_leg_state.shoulder_angle, -1.0, 1.0,
                                                     MIN_SERVO_ANGLE, MAX_SERVO_ANGLE);
  out.bl_leg_state.elbow_angle    = mapf_constrained(norm_pose.bl_leg_state.elbow_angle, -1.0, 1.0,
                                                     MIN_SERVO_ANGLE, MAX_SERVO_ANGLE);

  return out;
}

float median(float *values, int n)
{
  float tmp[n];

  for (int i = 0; i < n; i++) {
    tmp[i] = values[i];
  }

  for (int i = 1; i < n; i++) {
    float key = tmp[i];
    int j = i - 1;
    while (j >= 0 && tmp[j] > key) {
      tmp[j + 1] = tmp[j];
      j--;
    }
    tmp[j + 1] = key;
  }

  if (n % 2 == 0) {
    return 0.5f * (tmp[n/2 - 1] + tmp[n/2]);
  } else {
    return tmp[n/2];
  }
}

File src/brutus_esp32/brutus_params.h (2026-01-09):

/**
 * @file brutus_params.h
 * @brief Definition of Parameters for Brutus.
 *
 */

#ifndef BRUTUS_PARAMS__H
#define BRUTUS_PARAMS__H

#include "BrutusPose.h"

// --------- SERVOS CONFIG ----------

// Actual configuration is for MG90s servos
#define PWM_SERVO_FREQ 50

#define MIN_SERVO_ANGLE -90.0
#define MAX_SERVO_ANGLE 90.0

#define MIN_SERVO_PWM_PULSE_US 500
#define MAX_SERVO_PWM_PULSE_US 2500

// ---------------------------



// ---------- GPIOs -----------

#define US_R_TRIG 17
#define US_R_ECHO 5

#define US_L_TRIG 4
#define US_L_ECHO 16

#define US_F_TRIG 15
#define US_F_ECHO 2

#define R_PIN 32
#define G_PIN 25
#define B_PIN 33

#define PCA9685_OE 19

// ---------------------------



// --------- LEGS ----------

#define SHOULDER_BACK_LEFT_PCA_PIN 0
#define ELBOW_BACK_LEFT_PCA_PIN    1

#define SHOULDER_BACK_RIGHT_PCA_PIN 2
#define ELBOW_BACK_RIGHT_PCA_PIN    3

#define SHOULDER_FRONT_LEFT_PCA_PIN 9
#define ELBOW_FRONT_LEFT_PCA_PIN    8

#define SHOULDER_FRONT_RIGHT_PCA_PIN 13
#define ELBOW_FRONT_RIGHT_PCA_PIN    12



#define SHOULDER_BACK_LEFT_ANGLE_OFFSET -2.0
#define ELBOW_BACK_LEFT_ANGLE_OFFSET    -5.0

#define SHOULDER_BACK_RIGHT_ANGLE_OFFSET -6.0
#define ELBOW_BACK_RIGHT_ANGLE_OFFSET    0.0

#define SHOULDER_FRONT_LEFT_ANGLE_OFFSET -5.0
#define ELBOW_FRONT_LEFT_ANGLE_OFFSET    0.0 //-12.0

#define SHOULDER_FRONT_RIGHT_ANGLE_OFFSET -2.0
#define ELBOW_FRONT_RIGHT_ANGLE_OFFSET    -20.0


#define SHOULDER_BACK_LEFT_INVERTED false
#define ELBOW_BACK_LEFT_INVERTED    true

#define SHOULDER_BACK_RIGHT_INVERTED true
#define ELBOW_BACK_RIGHT_INVERTED    false

#define SHOULDER_FRONT_LEFT_INVERTED false
#define ELBOW_FRONT_LEFT_INVERTED    false

#define SHOULDER_FRONT_RIGHT_INVERTED true
#define ELBOW_FRONT_RIGHT_INVERTED    true

// ---------------------------

// -------- FreeRTOS -----------
#define MOTION_CORE  0
#define DEFAULT_MOTION_PERIOD 150 // [ms]
#define MOTION_TASK_SIZE 4096

#define LOGIC_CORE 1

#define MODES_PERIOD 200 // SAME PERIOD AS ALL LOGIC CORE TASKS
#define MODES_TASK_SIZE 4096

// -----------------------------


// ---------- PERCEPTION ----------
#define N_DISTANCE_SENSORS 3

#define PERCEPTION_PRIO 3

#define PERCEPTION_PERIOD 200 // [ms]
#define MIN_PERCEPTION_TIMEOUT 30 // [ms]
#define PERCEPTION_TASK_SIZE 4096
// --------------------------------

// ------- POSES ---------
constexpr BrutusLegState STANDING_FR_STATE {20, -20};
constexpr BrutusLegState STANDING_FL_STATE {20, -20};
constexpr BrutusLegState STANDING_BR_STATE {-20, -20};
constexpr BrutusLegState STANDING_BL_STATE {-20, -20};

constexpr BrutusPose STANDING_POSE {STANDING_FR_STATE,
                                    STANDING_FL_STATE,
                                    STANDING_BR_STATE,
                                    STANDING_BL_STATE};

#define ELBOW_UP 0
#define ELBOW_DOWN -20

#define FRONT_FORWARD_SHOULDER 60.0
#define FRONT_BACK_SHOULDER 30.0
#define FRONT_MID_SHOULDER (FRONT_FORWARD_SHOULDER + FRONT_BACK_SHOULDER) / 2.0

#define BACK_FORWARD_SHOULDER -20.0
#define BACK_BACK_SHOULDER -35.0
#define BACK_MID_SHOULDER (BACK_FORWARD_SHOULDER + BACK_BACK_SHOULDER) / 2.0

constexpr BrutusLegState FRONT_FORWARD_UP_STATE {FRONT_FORWARD_SHOULDER, ELBOW_UP};
constexpr BrutusLegState FRONT_FORWARD_DOWN_STATE {FRONT_FORWARD_SHOULDER, ELBOW_DOWN};

constexpr BrutusLegState BACK_FORWARD_UP_STATE {BACK_FORWARD_SHOULDER, ELBOW_UP};
constexpr BrutusLegState BACK_FORWARD_DOWN_STATE {BACK_FORWARD_SHOULDER, ELBOW_DOWN};

constexpr BrutusLegState FRONT_BACK_UP_STATE {FRONT_BACK_SHOULDER, ELBOW_UP};
constexpr BrutusLegState FRONT_BACK_DOWN_STATE {FRONT_BACK_SHOULDER, ELBOW_DOWN};

constexpr BrutusLegState BACK_BACK_UP_STATE {BACK_BACK_SHOULDER, ELBOW_UP};
constexpr BrutusLegState BACK_BACK_DOWN_STATE {BACK_BACK_SHOULDER, ELBOW_DOWN};

constexpr BrutusLegState FRONT_MID_UP_STATE {20,0};
constexpr BrutusLegState BACK_MID_UP_STATE {-20,20};

#define N_GAIT_STEPS 6

constexpr BrutusPose GAIT_1 {FRONT_FORWARD_DOWN_STATE,
                             FRONT_BACK_UP_STATE,
                             BACK_BACK_UP_STATE,
                             BACK_FORWARD_DOWN_STATE};

constexpr BrutusPose GAIT_2 {FRONT_BACK_DOWN_STATE,
                             FRONT_FORWARD_UP_STATE,
                             BACK_FORWARD_UP_STATE,
                             BACK_BACK_DOWN_STATE};

constexpr BrutusPose GAIT_3 {FRONT_BACK_DOWN_STATE,
                             FRONT_FORWARD_DOWN_STATE,
                             BACK_FORWARD_DOWN_STATE,
                             BACK_BACK_DOWN_STATE};

constexpr BrutusPose GAIT_4 {FRONT_BACK_UP_STATE,
                             FRONT_FORWARD_DOWN_STATE,
                             BACK_FORWARD_DOWN_STATE,
                             BACK_BACK_UP_STATE};

constexpr BrutusPose GAIT_5 {FRONT_FORWARD_UP_STATE,
                             FRONT_BACK_DOWN_STATE,
                             BACK_BACK_DOWN_STATE,
                             BACK_FORWARD_UP_STATE};
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

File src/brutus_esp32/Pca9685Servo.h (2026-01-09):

/**
* @file Pca9685Servo.h
* @brief Definition of the Pca9685Servo class.
*/

#ifndef PCA_9685_SERVO__H
#define PCA_9685_SERVO__H

#include <Wire.h>
#include <Adafruit_PWMServoDriver.h>

#define PCA9685_RESOLUTION  4096
#define PWM_PERIOD_US       20000.0f

class Pca9685Servo {

private:
  Adafruit_PWMServoDriver* pca; // PCA's controller object reference
  int pca_idx;                  // PCA's pin where the servo is connected

  float min_angle;              // The lowest angle value that the servo can reach
  uint16_t min_pwm;             // PWM value correspondant to min_angle

  float max_angle;              // The highest angle value that the servo can reach
  uint16_t max_pwm;             // PWM value corresponant to max_angle

  uint16_t init_pwm;            // PWM value for the angle in the middle

public:

  /**
   * @brief Constructor
   */
  Pca9685Servo() {}

  /**
    * @brief Initializes a Pca9685Servo object with the given parameters.
    *
    * This method sets up the servo to use the specified PCA9685 controller,
    * configures the PWM pin, pulse width limits, and angle limits. It also
    * calculates the initial PWM value corresponding to the midpoint angle.
    *
    * @param pca Pointer to the Adafruit_PWMServoDriver instance controlling the PCA9685.
    * @param pca_idx The PCA9685 channel/pin number where the servo is connected.
    * @param min_pwm_pulse_period Minimum PWM pulse width in microseconds for the servo.
    * @param max_pwm_pulse_period Maximum PWM pulse width in microseconds for the servo.
    * @param min_angle Minimum angle the servo can reach (degrees).
    * @param max_angle Maximum angle the servo can reach (degrees).
    */
    void 
    init(Adafruit_PWMServoDriver* pca,
         int pca_idx,
         int min_pwm_pulse_period,
         int max_pwm_pulse_period,
         float min_angle,
         float max_angle)
    {
      this->pca = pca;
      this->pca_idx = pca_idx;

      this->min_pwm = Pca9685Servo::us_to_pwm(min_pwm_pulse_period);
      this->max_pwm = Pca9685Servo::us_to_pwm(max_pwm_pulse_period);

      this->min_angle = min_angle;
      this->max_angle = max_angle;

      float init_angle = (this->min_angle + this->max_angle) * 0.5f; 

      this->init_pwm = Pca9685Servo::angle_to_pwm(init_angle, min_angle, max_angle, this->min_pwm, this->max_pwm);
    }

  /**
   * @brief Sends a PWM pulse corresponding to an angle to the specified servo
   * 
   * @param angle   Desired angle, normalized to [this->min_angle, this->max_angle]
   * @param on_tick The tick when the PCA send the pulse to the servo
   */
  void set_angle(float angle,
                 uint16_t on_tick = 0)
  {
    float ang = this->normalize_to_servo_range(angle);

    uint16_t pwm_value = Pca9685Servo::angle_to_pwm(ang,
                                                    this->min_angle,
                                                    this->max_angle,
                                                    this->min_pwm,
                                                    this->max_pwm);
    this->pca->setPWM(this->pca_idx,
                      on_tick,
                      pwm_value);
  }

  /**
   * @return Actual servo's angle.
   */
  float
  get_angle()
  {
    uint16_t on_tick = this->pca->getPWM(this->pca_idx, false);
    uint16_t off_tick = this->pca->getPWM(this->pca_idx, true);

    uint16_t pwm_val;
    if (off_tick >= on_tick) {
      pwm_val = off_tick - on_tick;
    } else {
      pwm_val = off_tick + 4096 - on_tick;
    }

    float angle = Pca9685Servo::pwm_to_angle(pwm_val,
                                             this->min_pwm,
                                             this->max_pwm,
                                             this->min_angle,
                                             this->max_angle);

    return angle;
  }

  /**
   * @brief Wraps an angle into the servo's valid range.
   *
   * Normalizes the input angle so it fits within [min_angle, max_angle].
   *
   * @param angle Input angle in degrees.
   * @return float Normalized angle within the servo range.
   */
  float
  normalize_to_servo_range(float angle) {
    float range = this->max_angle - this->min_angle;
    float a = fmod(angle - this->min_angle, range);
    if (a < 0) a += range;
    return a + this->min_angle;
  }

  /**
   * @brief Converts a pulse width in microseconds to a PWM value for the PCA9685.
   *
   * The PCA9685 uses a 12-bit resolution (0-4095) to generate the PWM signal.
   * This function converts a pulse width in microseconds to the corresponding
   * register value to send to the PCA9685.
   *
   * @param pulse_width_us Desired pulse width in microseconds (us).
   * @return uint16_t PWM value corresponding to the pulse width, clamped to [0, 4095].
   *
   * @note Values below 0 are clamped to 0.
   * @note Values above 4095 are clamped to the maximum allowed.
   */
  static uint16_t
  us_to_pwm(float pulse_width_us)
  {
    float counts = (pulse_width_us / PWM_PERIOD_US) * PCA9685_RESOLUTION;

    if (counts < 0) counts = 0;
    if (counts > (PCA9685_RESOLUTION - 1)) counts = PCA9685_RESOLUTION - 1;

    return (uint16_t)counts;
  }

  /**
   * @brief Converts an angle to a PWM value for the PCA9685.
   *
   * This function maps the servo angle linearly to the corresponding PWM value.
   * It is useful to send position commands in human-understandable units (degrees).
   *
   * @param angle Desired angle for the servo.
   * @param min_angle Minimum achievable angle of the servo.
   * @param max_angle Maximum achievable angle of the servo.
   * @param min_pwm PWM value corresponding to the minimum angle.
   * @param max_pwm PWM value corresponding to the maximum angle.
   * @return uint16_t PWM value corresponding to the desired angle.
   *
   * @note Angles below min_angle are clamped to min_angle.
   * @note Angles above max_angle are clamped to max_angle.
   * @note The angle-to-PWM mapping is linear.
   */
  static uint16_t
  angle_to_pwm(float angle,
               float min_angle, float max_angle,
               uint16_t min_pwm, uint16_t max_pwm)
  {
    if (angle < min_angle) angle = min_angle;
    if (angle > max_angle) angle = max_angle;

    float slope = (float)(max_pwm - min_pwm) / (max_angle - min_angle);

    return (uint16_t)(min_pwm + slope * (angle - min_angle));
  }
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

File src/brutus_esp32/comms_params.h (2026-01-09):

/**
 * @file comms_params.h
 * @brief Definition of Parameters for comms.
 *
 */

#ifndef MQTT_PARAMS__H
#define MQTT_PARAMS__H

#include "BrutusPose.h"
#include "comms_structs.h"
#include "brutus_params.h"


// ----------- CLIENT ID -----------
#define CLIENT_ID "brutus_esp"

// ----------- TOPICS SUBS-----------

#define TOPIC_CMD_MODE   "brutus/cmd/mode"
#define TOPIC_CMD_VEL   "brutus/cmd/velocity"
#define TOPIC_CMD_POSE   "brutus/cmd/pose"

#define CMD_MODE   0
#define CMD_VEL    1
#define CMD_POSE   2

// ----------- TOPICS PUBS-----------

#define TOPIC_STATE_HEARTBEAT "brutus/data/heartbeat"
#define TOPIC_POSE            "brutus/data/pose"
#define TOPIC_DIST      "brutus/data/distance"

#define STATE_HEARTBEAT 0
#define POSE            1
#define DIST            2

// ----------- WAITS -----------
#define WIFI_WAIT 500
#define RECONNECT_WAIT 3000

// ----------- MODES -----------
#define IS_EDUROAM false // true to connect to eduroam, false to connect to normal wifi

// ----------- RANGES FOR TEST_WITH_RANDOM_MSG-----------
#define MIN_LEG_DEG 0
#define MAX_LEG_DEG 181

#define MIN_DIST 0
#define MAX_DIST 200

// ----------- JOINTS -----------
#define SHOULDER "0"
#define ELBOW "1"

// ----------- BUFFERS -----------
#define MSG_BUFFER 254
#define JSON_BUFFER 300

// ----------- FreeRTOS -----------
#define COMMS_PRIO 1
#define COMMS_PERIOD 200
#define COMMS_CORE LOGIC_CORE
#define BAUD 115200

// ----------- START CMD AND DATA -----------
constexpr BrutusLegState START_CMD_LEG {0.0, 0.0};
constexpr BrutusPose START_CMD_POSE {START_CMD_LEG, START_CMD_LEG, START_CMD_LEG, START_CMD_LEG};
constexpr BrutusCommsCmd START_CMD {0, 0.0, 0.0, START_CMD_POSE};

constexpr BrutusCommsData START_DATA {STANDING_POSE, 0.0, 0.0, 0.0};

#endif

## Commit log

2025-10-16 Electronic design version 1.0
    [aracnic_robot_circuit.fzz]
2025-10-17 leds and switch added
    [aracnic_robot_circuit.fzz, brutus_circuit.fzz]
2025-10-28 URDF for simulation and pybullet code template
    [brutus.urdf]
2025-10-28 Added ros2 package for brutus
    [Robot_controllers.yaml, brutus.urdf, brutus_copy.urdf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]
2025-11-15 fritzing update
    [brutus_circuit.fzz]
2025-11-18 Updated circuit
    [brutus_circuit.fzz]
2026-01-02 Meshes added
    [battery_limit_mesh.stl, chasis_cover_mesh.stl, chasis_mesh.stl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]
2026-01-09 Added most of the project
    [Robot_controllers.yaml, battery_height.csv, brutus.urdf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]
